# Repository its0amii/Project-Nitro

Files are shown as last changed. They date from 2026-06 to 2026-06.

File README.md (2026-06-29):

# Project-Nitro 🏎️💨

### FPV RC Racing Car with Game Effects

Have you ever wondered about having a **FPV RC Racing Car** with game effects such as:
- Boost
- Gun
- Health
- Drift (Bad effects and more)

Well, I have made this with the help of **NFC TAGS**. How it works is simple: when each car has an NFC reader underneath, and when it passes over a NFC tag, it will detect the code and look for what power or bad effect it is. Then I can pull that effect whenever we want. Beat your opponent and win with super powers using our own strategy to win the game!

## Zine
[zine](/doc/zine.pdf)
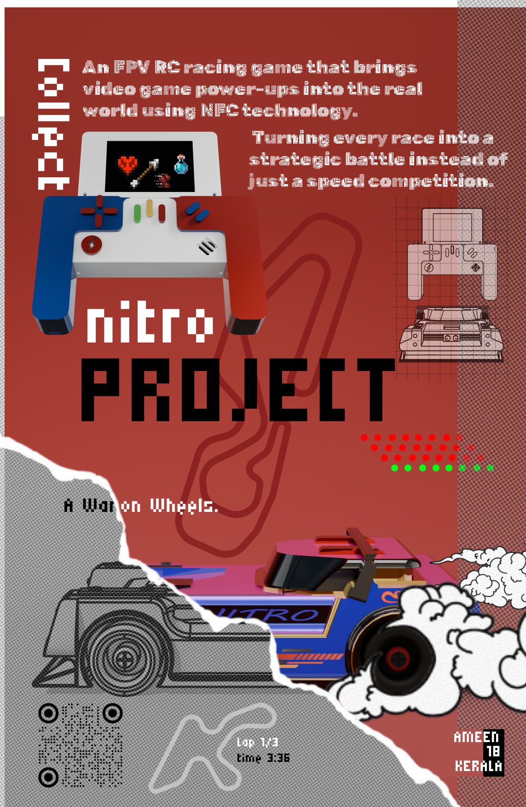
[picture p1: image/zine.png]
zine

## Photos of Car and Remote 📸

### Car Pics

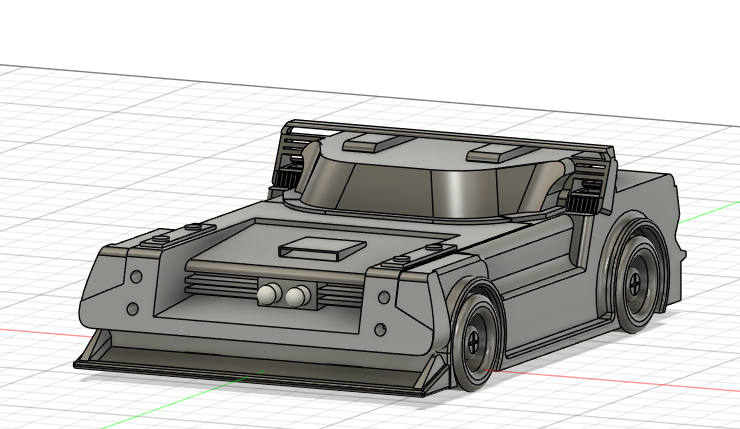
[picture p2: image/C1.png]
Car
  
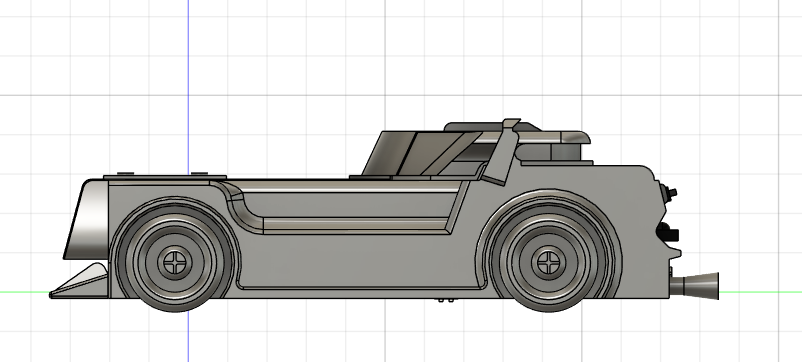
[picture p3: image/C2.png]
Car 2
  
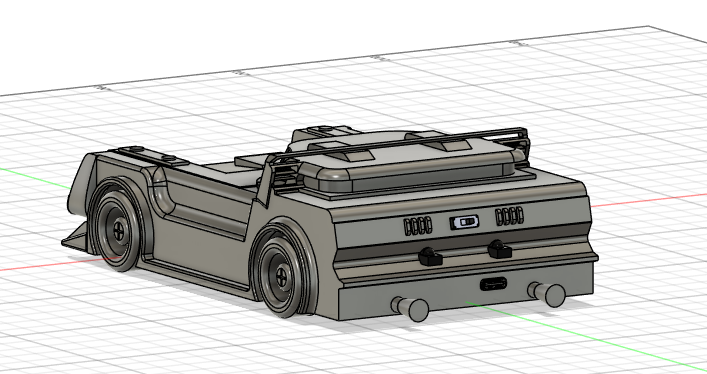
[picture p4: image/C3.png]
Car 3


### Remote

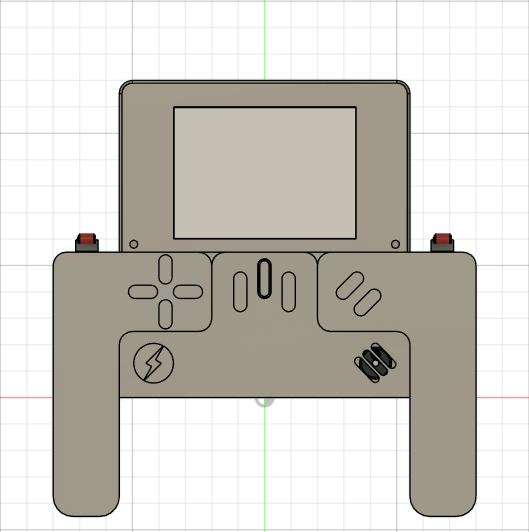
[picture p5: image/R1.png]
Remote
  
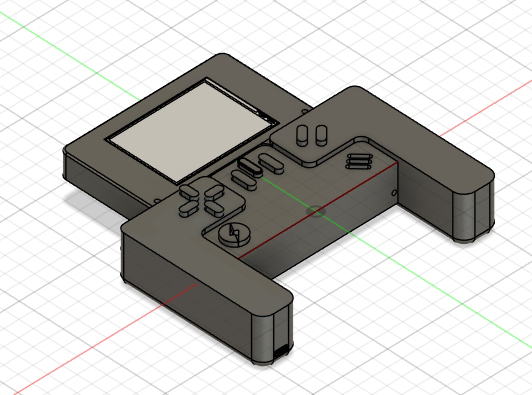
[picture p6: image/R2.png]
Remote 2
  
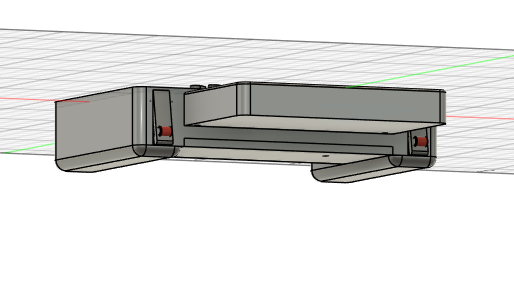
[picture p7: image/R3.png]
Remote 3

## Circuit Diagram

### Car PCB

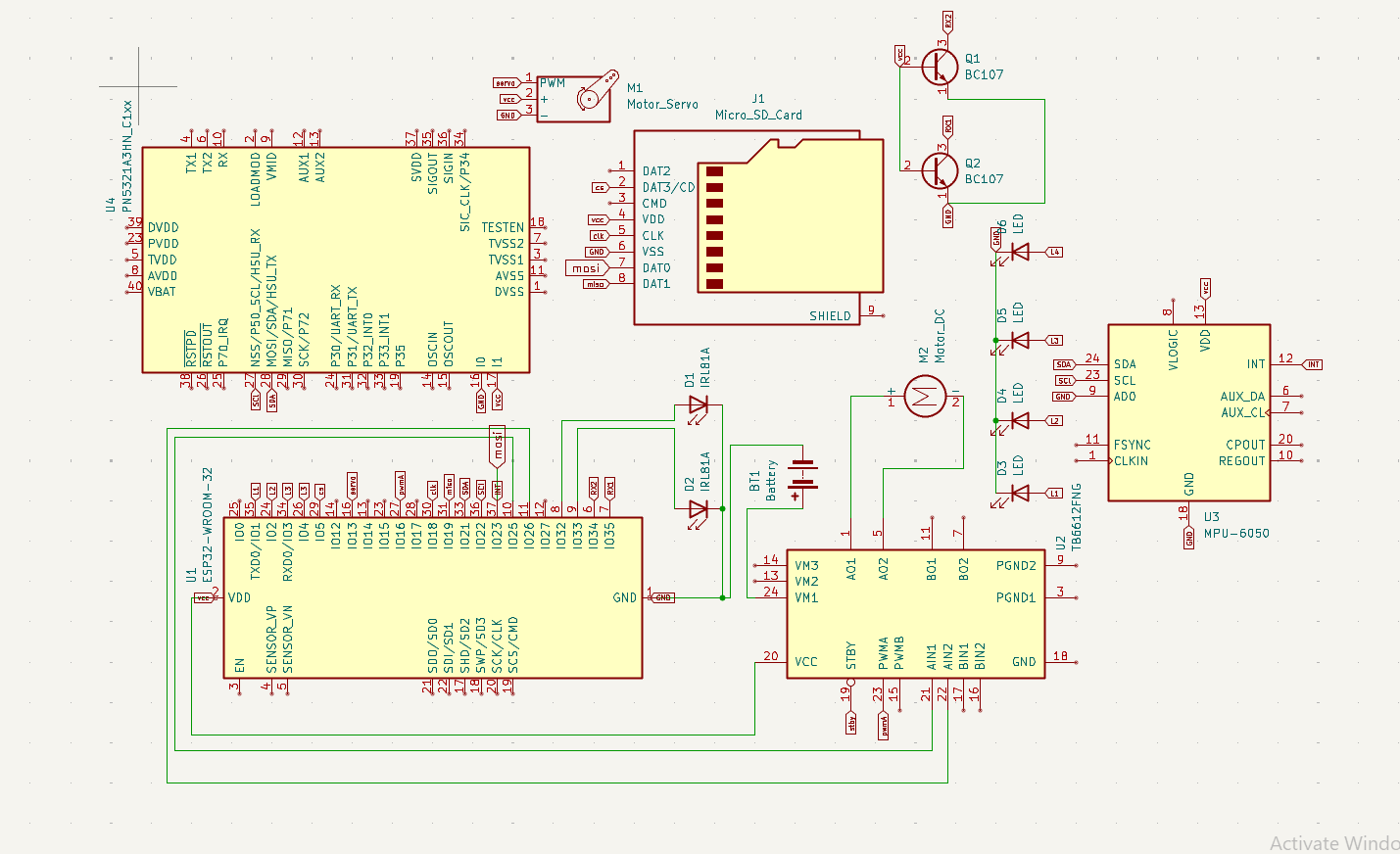
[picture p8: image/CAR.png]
Car PCB


### Remote PCB

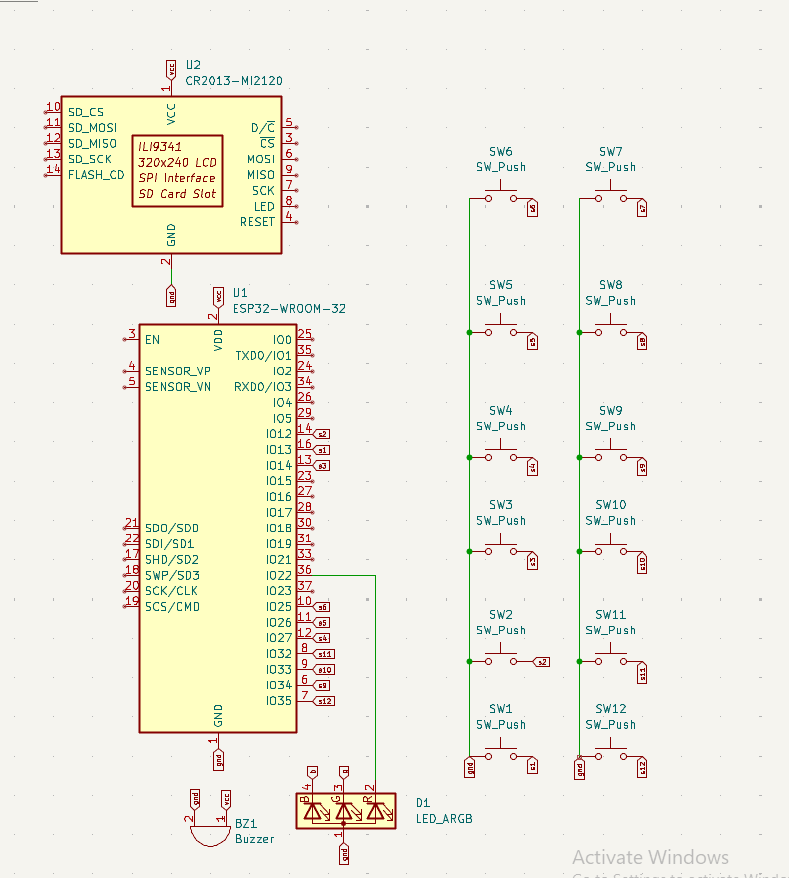
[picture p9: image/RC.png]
Remote PCB
  
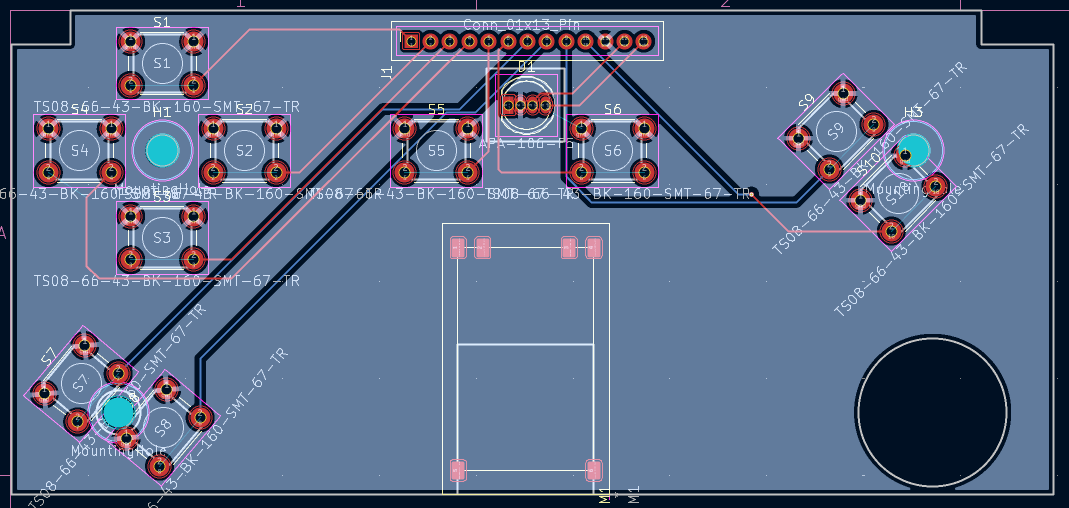
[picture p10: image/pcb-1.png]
PCB 1
  
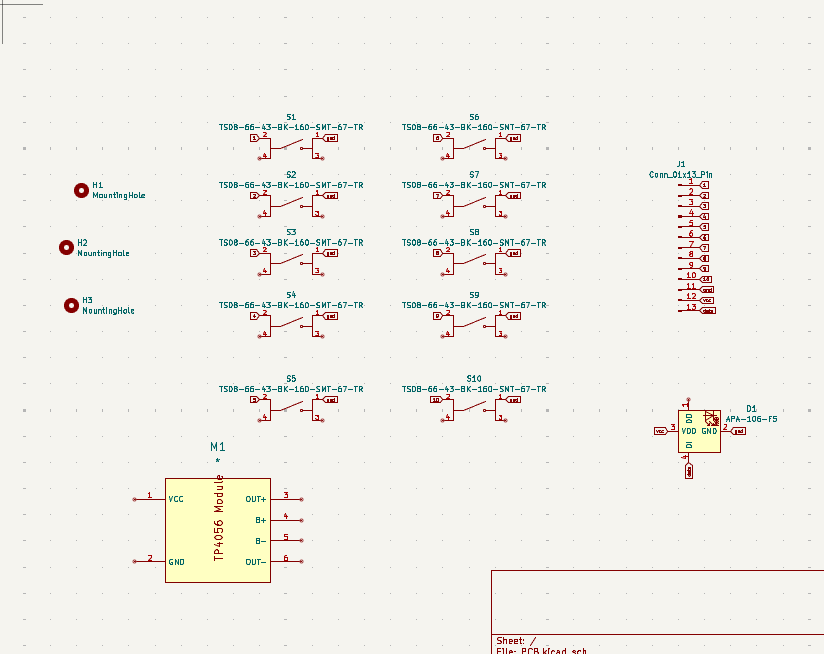
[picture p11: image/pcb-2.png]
PCB 2


## Motivation

I have always wondered to play **RC car** like in games with boost, power, win, health etc.. because that all make more fun for the world and playing with friends makes it even more fun. So I built this car - it will give you a game vibe with RC FPV cars in real life, bringing more fun and joy to the world!
## How to Build 🛠️

### Car Assembly

After 3D printing, check the tolerance of each part and sand it smoothly for better look and placement. Then solder everything with wires, place each component in its designated position as shown in the `.step` files, glue the IR receiver and transmitter, tape or glue the batteries in their places, place ESP32 on the ESP tray and screw it well, then mount to the car body as shown.
## Car Assembly

1. 3D print all STL files from `/cad/car`.
2. Sand the parts until they fit smoothly.
3. Insert all M3 heat inserts
4. Mount the N20 motor using two M3 screws.
5. Install the steering servo.
6. Mount the ESP32.
7. Install the PN532 NFC module.
8. Connect all electronics according to wiring diagram.
9. Mount FPV cam.
10. Install battery
11. scraw body

### Remote Assembly
## Car Assembly

1. 3D print all STL files from `/cad/remote`.
2. Sand the parts until they fit smoothly.
3. Insert all M3 heat inserts.
4. place the batter.
5. Mound the ESP32.
6. Mount PCB after soldering all switchs and LED.
7. Insert the button.
8. Connect all electronics according to wiring diagram.
9. Slide in the sreen and screw.
10. Slide the bottom case.
11. Close body.

After 3D printing, check the tolerance of each part and sand it smoothly for better look and placement. Then solder everything with wires, place the battery first followed by ESP32, solder the switch to PCB and connect the GPIOs Don't forget to place the LCD screen holders to screw for better holding, slide down the bottom part and screw it also then paint everything.

## How to Play/Setup 🎮

When you turn on the remote and car, it will connect (if it's your first time,you may need to pair them) You'll get a web interface in phone or laptop for FPV. Once connected you have two modes:

### Free Ride Mode
You can drive it as normal RC car without any special features.

### Race Mode  
In this mode, you need an opponent to play with. One of you will host the game and that person's car becomes the controller of the game also. The remote looks for players  when a player is found:
- Flip the car and reegister all NFC tags again
- Accept the win gate tag and pit lane
- Place everthing in place as you want
- Everywhere, you can make your own track with anything you have
- Play and win the game
## Game Effects ⚡

### Good Power-ups
- **Boost** - Speed boost to move faster  
- **Health** - Get more health  
- **Shield** - Protection from enemy bullets  
- **Bullets** - Shoot projectiles  

### Bad Effects
- **Drift** - The car gets drift randomly  
- **Random Control** - Controls switch randomly (forward becomes backward)  
- **Slowness** - Car goes slowly  
- **Damage** - Low health  

### Bonus Feature
All bad effects can be cleared by going to your own pit lane.
## How It Works ⚙️

This all works with ESP-NOW protocol. The host's car maintains the rules and everything:

- `car ↔ remote` - Direct communication between each unit  
- `car(host) ↔ car(client)` - Host communicates with client cars  
- `camera → WiFi web → phone, laptop...` - Video stream to viewer devices

## Folder Structure 📁
```
cad/

├── car/
│   └── car.step

├── remote/
│   └── Remote.step

├── nfc/
│   └── nfc tag sticker.step

firmware/

├── car/
│   └── Car firmware

├── remote/
│   └── Remote firmware

├── camera/
│   └── FPV camera firmware
```

### Car Section
- [Car CAD](/cad/car/) - 3D models and designs  
- [Car Firmware](/firmware/car/) - Embedded code for the Car  
- [FPV Camera](/firmware/car_cam/) - Camera firmware  
- [Car Circuit](/circuit/car/) - Schematic diagrams  

### Remote Section
- [Remote CAD](/cad/remote/) - 3D models and designs  
- [Remote Firmware](/firmware/remote/) - Embedded code for the remote  
- [Remote circuit](/circuit/remote/) - Schematic diagrams

## BOM (Bill of Material)
[BOM](/doc/BOM.csv.csv)

## Car Components 🛒

|**Item**|Number|Approx. Price|Link|
|---|---|---|---|
|5mm 940nm IR Emitter Transmitter|2|₹140|[Amazon](https://amzn.in/d/03gj3whx)|
|MPU6050 IMU|1|₹174|[Amaz](https://amzn.in/d/0gS9H64g)|
|PN532 NFC RFID Module|1|₹425|[Robokit](https://robokits.co.in/wireless-solutions/rfid/pn532-nfc-rfid-module-v3-kit-reader-writer-breakout-board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)|
|ESP32S3-Sense|1|₹1800|[SeeedStudio](https://www.seeedstudio.com/XIAO-ESP32S3-Sense-p-5639.html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)|
|ESP32 WiFi Bluetooth|1|₹299|[Amazon](https://amzn.in/d/0fkaqaUV)|
|6V N20 600 RPM Motor|1|₹149|[Robocraz](https://robocraze.com/products/6v-n20-600-rpm-miniature-gear-motor)|
|3.7V 2500mAh 18650 Li-Ion Battery|2|₹500|[Robocraze](https://robocraze.com/products/3-7v-2500mah-18650-li-ion-battery)|
|TP4056 Type-C Mini Charger|1|₹49|[Robocraz](https://robocraze.com/products/tp4056-battery-charger-c-type-module-with-protection-1)|
|LM2596 DC-DC Buck Converter|1|₹79|[Robocraze](https://robocraze.com/products/lm2596-dc-dc-buck-module)|
|SG90 Micro Servo Motor|1|₹99|[robocraze](https://robocraze.com/products/sg90-micro-servo-motor)|
|DRV8833 2-Channel Driver|1|₹99|[Robocraze](https://robocraze.com/products/drv8833-2-channel-dc-motor-driver)|
|TSOP38238 IR Receiver Diode|2|₹50|[QuartzComponents](https://quartzcomponents.com/products/tsop38238-ir-receiver-diode-38khz)|
|M3x4mm Heat Set Inserts|20|₹80|[Robu](https://robu.in/product/m3-x-4-mm-brass-heat-set-knurl-threaded-round-insert-nut-25-pcs/)|
|M3 x 6mm Screw|20|₹60|[RoboticsDNA](roboticsdna.in/product/m3-x-6mm-bolt-ss-304-csk-countersunk-philips-head-25-pcs/)|

#### Approximate Car Cost: **₹4,000**

### Remote

|**Item**|Number|Approx. Price|Link|
|---|-----|---|---|
|ESP32 WiFi Bluetooth|1|₹299|[Amazon](https://amzn.in/d/03HUoLg3)|
|Tactile momentary push button|12|₹36|[amazon](https://amzn.in/d/093r9Vyk)|
|3.7V 1500mAh LiPo Rechargeable Battery Model|1|₹350|[robocraze](https://robocraze.com/products/3-7v-1500mah-lipo-rechargeable-battery-model-uk-523450p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)|
|TP4056 Type-C Mini|1|₹49|[robocraze](https://robocraze.com/products/tp4056-battery-charger-c-type-module-with-protection-1)|
|3.3V Small Piezo Buzzer|1|₹30|https://robocraze.com/products/3-volts-buzzer-small|
|5mm Common Anode RGB LED 4Pin Through Hole White Diffused LED|1|₹15|[robocraze](https://robocraze.com/products/5mm-common-anode-rgb-led-4pin-pack-of-10)|
|2.8 Inch TFT LCD Display|1|₹780|[robocraze](https://robocraze.com/products/smartelex-2-8-inch-tft-lcd-display-240x320-color-lcd-screen-for-diy-electronics)|
|m3x4mm heat set inserts|12|₹80|[Rubu](https://robu.in/product)|m3-x-4-mm-brass-heat-set-knurl-threaded-round-insert-nut-25-pcs/|
|M3 x 6mm screw|12|₹60|[RoboticsDNA](roboticsdna.in/product/m3-x-6mm-bolt-ss-304-csk-countersunk-philips-head-25-pcs/)
#### Approximate Remote Cost
**₹1700**

### Total Approximate Cost

|Part|Cost|
|-----|-----|
|Car|₹4000|
|Remote|₹1700|

# Future Upgrade ⏫

* Leader Board 
* Anti-Cheat
* challenge etc

Thats it for now.
> **NOTE:** you need to place a black transparent plastic thin sheet or something on the front window where the camera is placed and in the remote for the switch you can either use this Prototyping PCB or you can custom print a pcb board everything on car and remote is either snap fit or screwable and only the led , ir and batter need glue-gun/tap

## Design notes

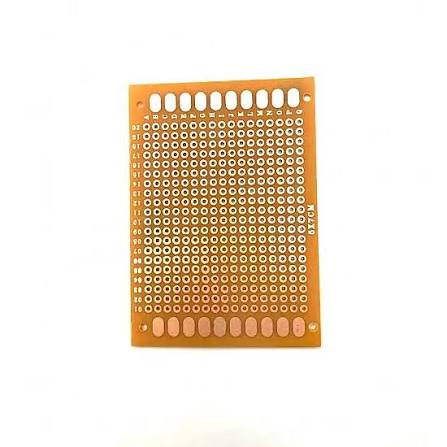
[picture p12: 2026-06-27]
image/image.png

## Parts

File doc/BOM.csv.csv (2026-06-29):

Category | Item | Quantity | Approx_Price_INR | Link
Car | 5mm 940nm IR Emitter Transmitter | 2 | 140 | https://amzn.in/d/03gj3whx
Car | MPU6050 IMU | 1 | 174 | https://amzn.in/d/0gS9H64g
Car | PN532 NFC RFID Module | 1 | 425 | https://robokits.co.in/wireless-solutions/rfid/pn532-nfc-rfid-module-v3-kit-reader-writer-breakout-board
Car | ESP32S3-Sense | 1 | 1800 | https://www.seeedstudio.com/XIAO-ESP32S3-Sense-p-5639.html
Car | ESP32 WiFi Bluetooth | 1 | 299 | https://amzn.in/d/0fkaqaUV
Car | 6V N20 600 RPM Motor | 1 | 149 | https://robocraze.com/products/6v-n20-600-rpm-miniature-gear-motor
Car | 3.7V 2500mAh 18650 Li-Ion Battery | 2 | 500 | https://robocraze.com/products/3-7v-2500mah-18650-li-ion-battery
Car | TP4056 Battery Charger | 1 | 49 | https://robocraze.com/products/tp4056-battery-charger-c-type-module-with-protection-1
Car | LM2596 DC-DC Buck Converter | 1 | 79 | https://robocraze.com/products/lm2596-dc-dc-buck-module
Car | SG90 Micro Servo Motor | 1 | 99 | https://robocraze.com/products/sg90-micro-servo-motor
Car | DRV8833 Motor Driver | 1 | 99 | https://robocraze.com/products/drv8833-2-channel-dc-motor-driver
Car | TSOP38238 IR Receiver Diode | 2 | 50 | https://quartzcomponents.com/products/tsop38238-ir-receiver-diode-38khz
Car | M3x4mm Heat Set Inserts | 20 | 50
Car | M3x6mm Screws | 20 | 50
Remote | ESP32 WiFi Bluetooth | 1 | 299 | https://amzn.in/d/03HUoLg3
Remote | Tactile Momentary Push Button | 12 | 36 | https://amzn.in/d/093r9Vyk
Remote | 3.7V 1500mAh LiPo Battery | 1 | 350 | https://robocraze.com/products/3-7v-1500mah-lipo-rechargeable-battery-model-uk-523450p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
Remote | TP4056 Battery Charger | 1 | 49 | https://robocraze.com/products/tp4056-battery-charger-c-type-module-with-protection-1
Remote | 3.3V Small Piezo Buzzer | 1 | 30 | https://robocraze.com/products/3-volts-buzzer-small
Remote | 5mm Common Anode RGB LED | 1 | 15 | https://robocraze.com/products/5mm-common-anode-rgb-led-4pin-pack-of-10
Remote | 2.8 Inch TFT LCD Display | 1 | 780 | https://robocraze.com/products/smartelex-2-8-inch-tft-lcd-display-240x320-color-lcd-screen-for-diy-electronics
Remote | M3x4mm Heat Set Inserts | 12 | 30
Remote | M3x6mm Screws | 12 | 30
SUMMARY | Car Total |  | 3963
SUMMARY | Remote Total |  | 1619
SUMMARY | Grand Total |  | 5582

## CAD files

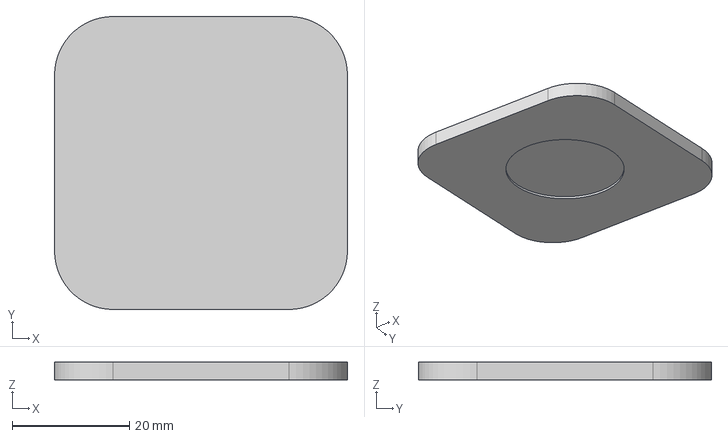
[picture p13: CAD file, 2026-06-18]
cad/nfc/nfc tag sticker.step
50.0 x 50.0 x 3.00 mm

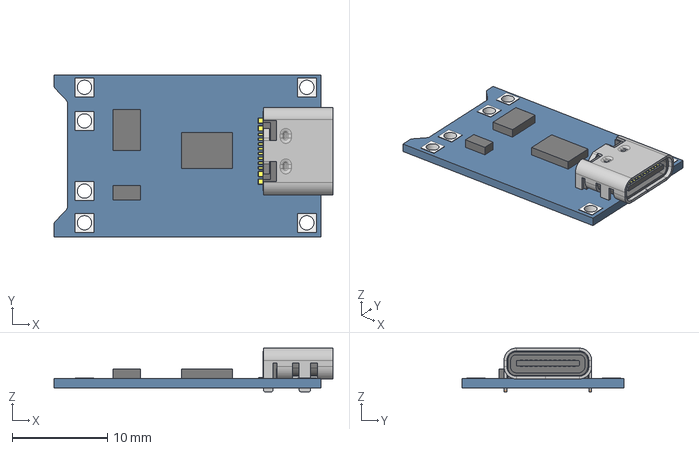
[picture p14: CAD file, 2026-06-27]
pcb/rc/footprint-symbol/TP4056--3DModel-STEP-684600.STEP
29.3 x 17.0 x 4.60 mm

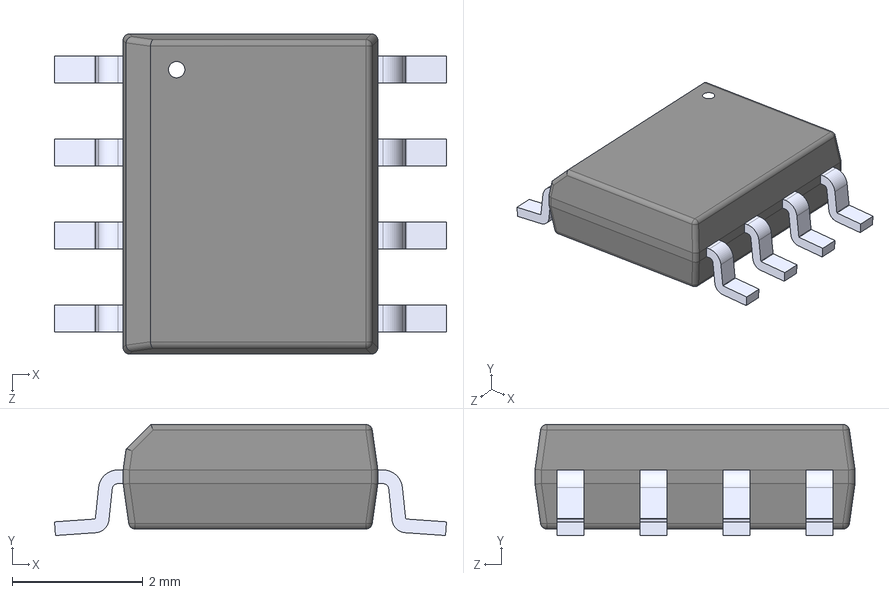
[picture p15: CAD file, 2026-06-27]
pcb/rc/footprint-symbol/TP4056/TP4056.step
6.00 x 1.70 x 4.90 mm

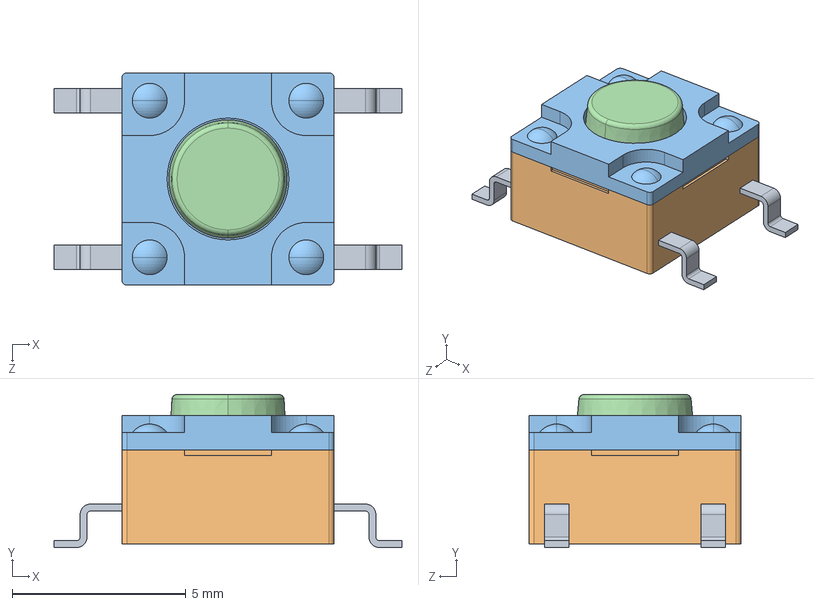
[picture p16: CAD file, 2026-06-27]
pcb/rc/footprint-symbol/TS08-66-43-BK-160-SMT-67-TR/TS08-66-43-BK-160-SMT-67-TR.step
10.0 x 4.40 x 6.10 mm

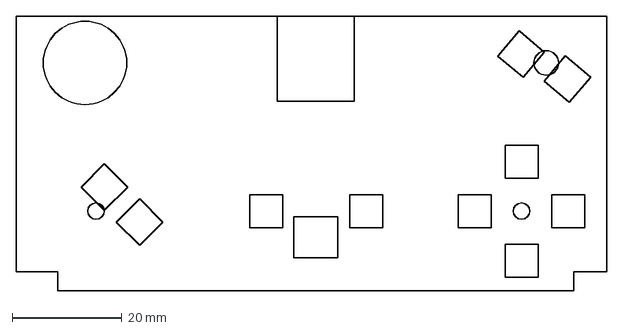
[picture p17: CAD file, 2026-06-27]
pcb/rc/Sketch.dxf
107.5 x 50.0 mm

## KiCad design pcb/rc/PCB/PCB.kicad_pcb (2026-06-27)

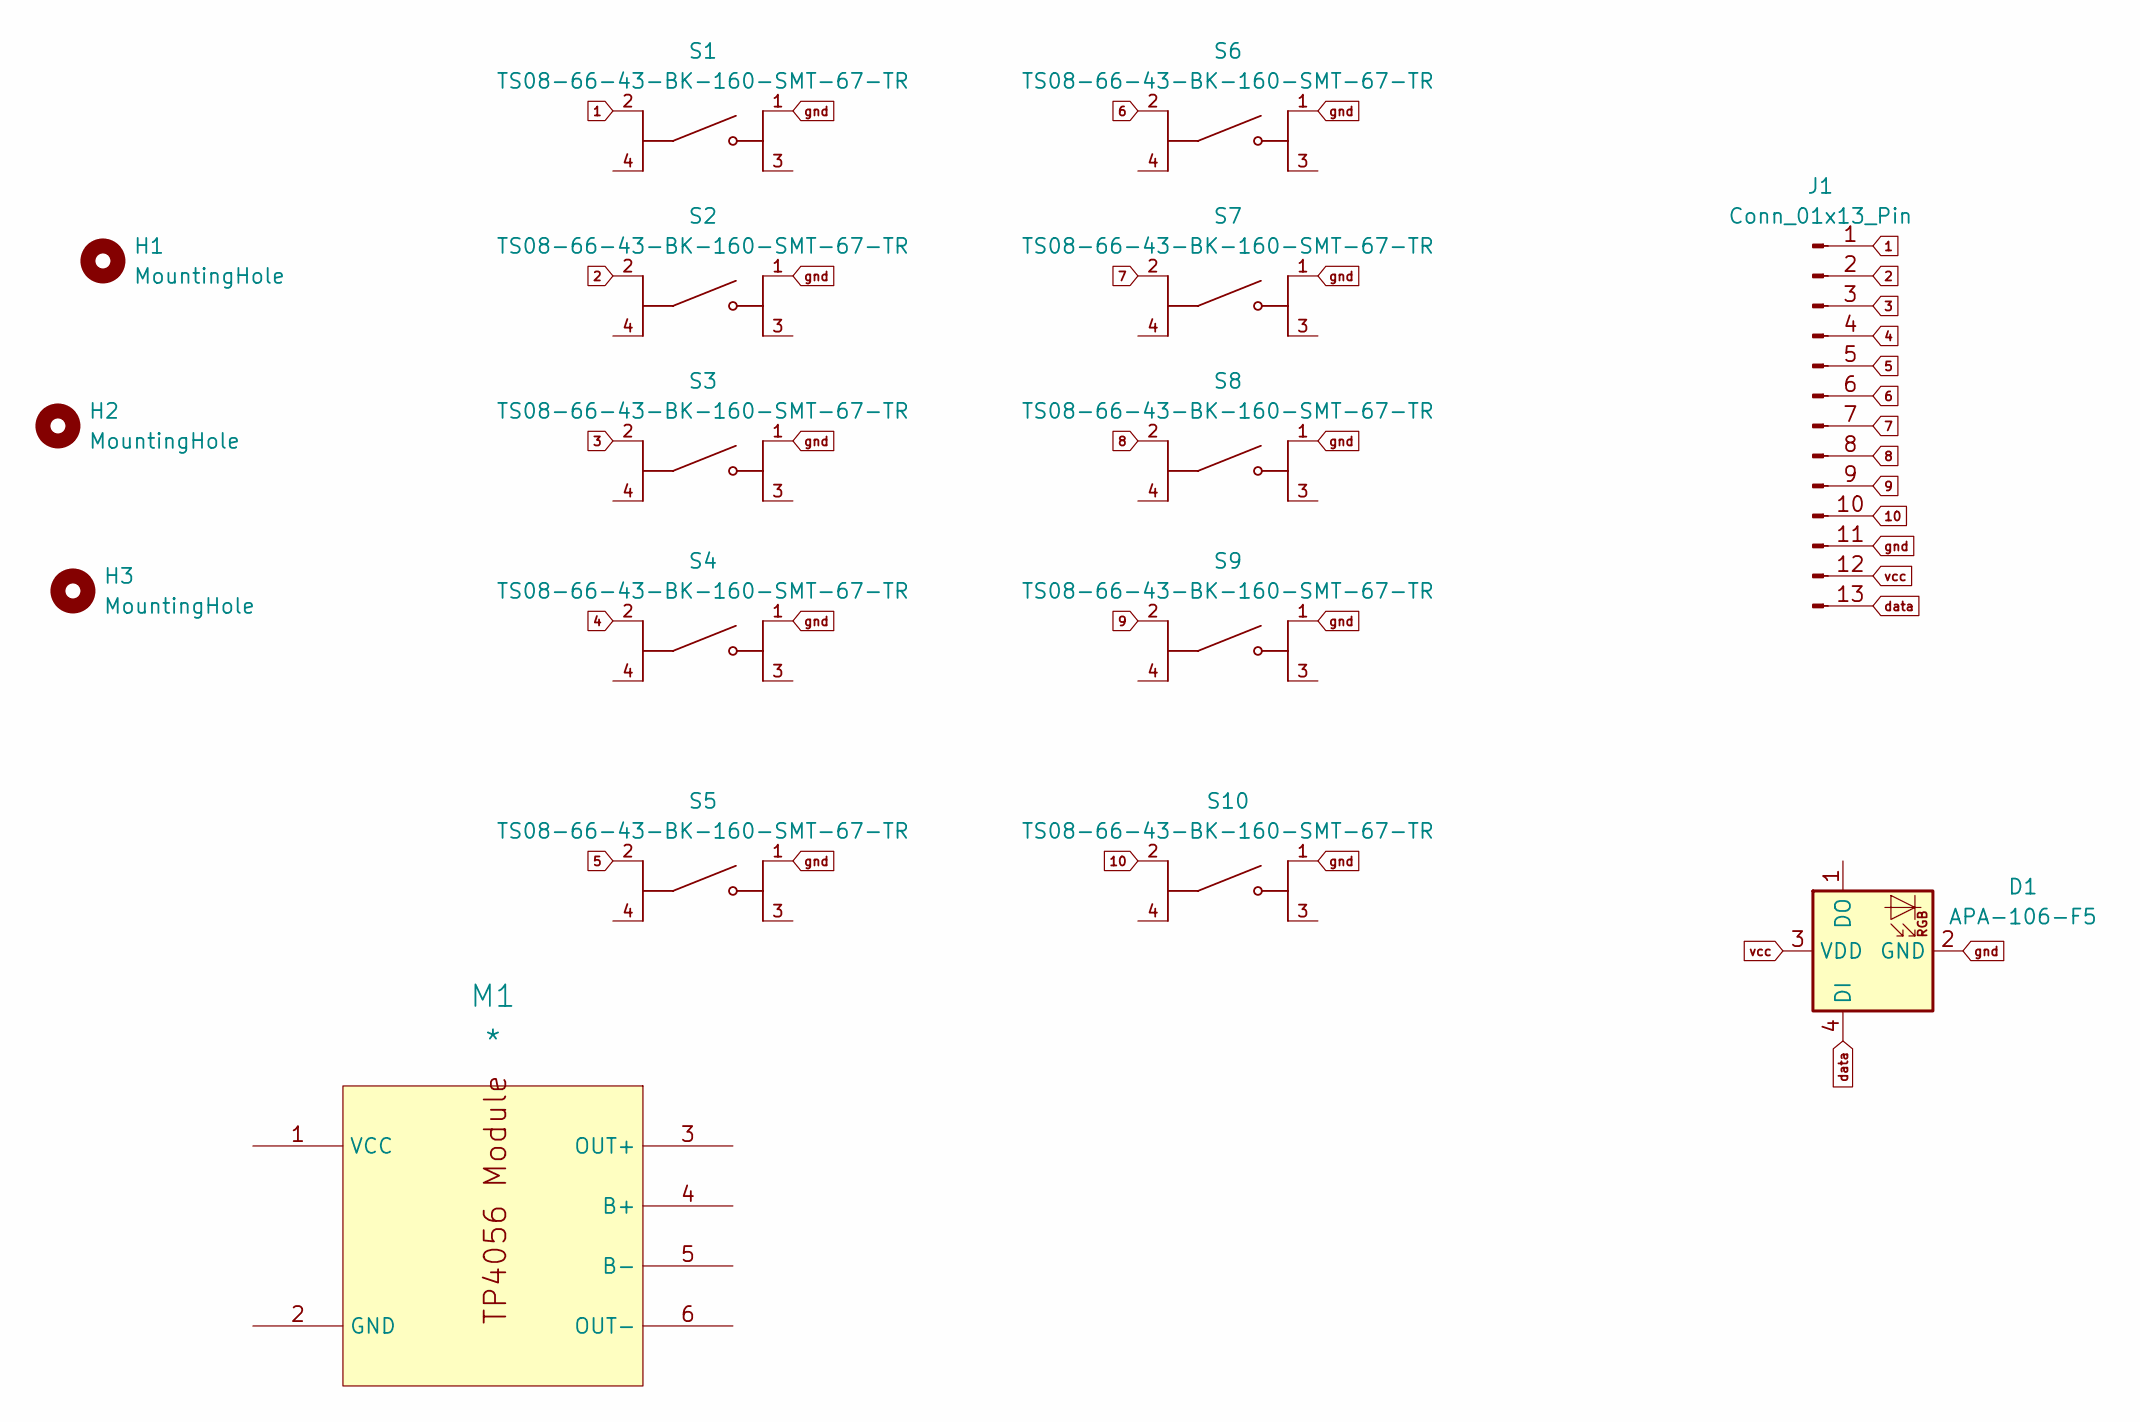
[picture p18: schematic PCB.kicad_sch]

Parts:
D1: APA-106-F5; LED_D5.0mm-4_RGB
H1, H2, H3: MountingHole; MountingHole_3mm
J1: Conn_01x13_Pin; PinSocket_1x13_P2.00mm_Horizontal
M1: *; tp4056
S1, S2, S3, S4, S5, S6, S7, S8, S9, S10: TS08-66-43-BK-160-SMT-67-TR; SW_PUSH_6mm; PARTREV 1.03

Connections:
1: J1.1, S1.2
2: J1.2, S2.2
3: J1.3, S3.2
4: J1.4, S4.2
5: J1.5, S5.2
6: J1.6, S6.2
7: J1.7, S7.2
8: J1.8, S8.2
9: J1.9, S9.2
10: J1.10, S10.2
data: D1.4 (DI), J1.13
gnd: D1.2 (GND), J1.11, S1.1, S2.1, S3.1, S4.1, S5.1, S6.1, S7.1, S8.1, S9.1, S10.1
vcc: D1.3 (VDD), J1.12

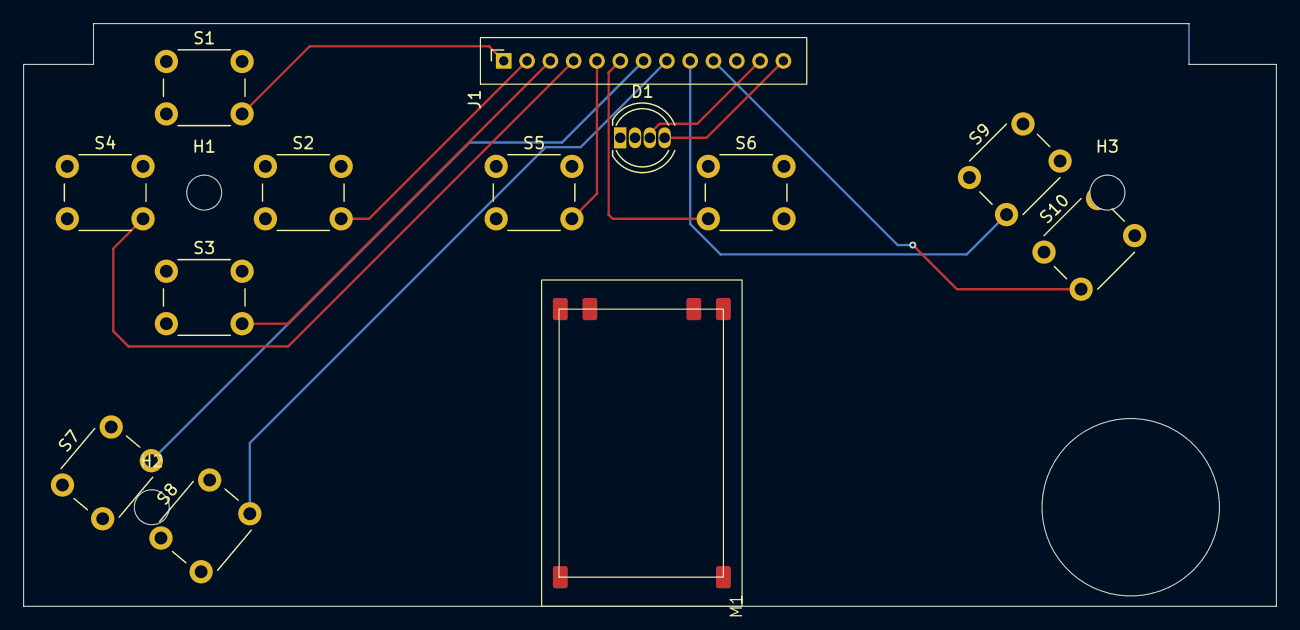
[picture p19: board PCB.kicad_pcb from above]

Board: 2 copper layers, 107.5 x 50.0 mm, 16 parts (0 on the bottom side), 13 nets.

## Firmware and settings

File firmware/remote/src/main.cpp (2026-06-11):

// =============================================================================
//  main.cpp — FPV Racer v2.0 RC Firmware
//
//  ESP32 30-pin, 2.8" ILI9341 TFT (SPI), 12 buttons
//
//  Core 0 (app_cpu): loop() — ESP-NOW receive, phase state machine,
//                             button events, display updates
//  Core 1 (pro_cpu): driveTask — 50Hz drive packet sender
//
//  Power-on sequence:
//    1. MCU wakes → PWR_LATCH HIGH (holds own power via P-MOSFET)
//    2. Splash screen
//    3. Attempt to connect to paired car (stored MAC in NVS)
//    4. RC_IDLE / RC_FREE_DRIVE
//    5. CONNECT button → RC_LOOKING → pairing → lobby → race
// =============================================================================

#include <Arduino.h>
#include <WiFi.h>
#include <esp_now.h>
#include <Preferences.h>
#include <freertos/FreeRTOS.h>
#include <freertos/task.h>
#include <freertos/queue.h>
#include <freertos/semphr.h>

#include "rc_types.h"
#include "buttons.h"
#include "rc_display.h"

// ---------------------------------------------------------------------------
// Global state
// ---------------------------------------------------------------------------
static RCPhase      g_phase       = RC_IDLE;
static RCGameState  g_gs          = {};
static bool         g_carConnected= false;
static bool         g_isHost      = false; // RC paired to host car?

// Peer MACs
static uint8_t g_ownMac[6]    = {};
static uint8_t g_carMac[6]    = {};      // paired car
static uint8_t g_oppCarMac[6] = {};      // opponent car (host for validation)
static uint8_t g_oppRcMac[6]  = {};      // opponent RC
static bool    g_peersKnown   = false;

// Lobby settings (host RC only)
static uint8_t  g_lobbyMode  = 0;   // 0=LAP, 1=TIME
static uint8_t  g_lobbyLaps  = 5;
static uint16_t g_lobbyTimeSec = 180;
static uint8_t  g_lobbyTags  = 10;
static bool     g_myReady    = false;
static bool     g_oppReady   = false;

// Battery %
static uint8_t  g_battPct    = 100;

// Match end packet
static PktMatchEnd g_matchEnd = {};

// ---------------------------------------------------------------------------
// FreeRTOS
// ---------------------------------------------------------------------------
static QueueHandle_t     xRxQueue;      // ESP-NOW → Core 0
static SemaphoreHandle_t xDriveSem;     // Core 0 → Core 1: ok to send drive

// Drive command (written by Core 0, read by Core 1)
static volatile int8_t g_driveThrottle = 0;
static volatile int8_t g_driveSteering = 0;

// Last shoot time
static uint32_t g_lastShootMs = 0;

// Looking animation
static uint8_t  g_lookingDot  = 0;
static uint32_t g_lookingMs   = 0;
static uint32_t g_lookingStartMs = 0;

// NFC setup state (mirrored from car via UI updates)
static uint8_t g_nfcDone  = 0;
static uint8_t g_nfcTotal = 10;

// ---------------------------------------------------------------------------
// ESP-NOW helpers
// ---------------------------------------------------------------------------

static esp_now_peer_info_t s_peer = {};

static void espnow_add_peer(const uint8_t* mac) {
    memcpy(s_peer.peer_addr, mac, 6);
    s_peer.channel = 0;
    s_peer.encrypt = false;
    if (!esp_now_is_peer_exist(mac))
        esp_now_add_peer(&s_peer);
}

static void espnow_send(const uint8_t* mac, const void* data, size_t len) {
    if (esp_now_is_peer_exist(mac))
        esp_now_send(mac, (const uint8_t*)data, len);
}

static void espnow_broadcast(const void* data, size_t len) {
    // ESP-NOW broadcast MAC
    static const uint8_t bcast[6] = {0xFF,0xFF,0xFF,0xFF,0xFF,0xFF};
    esp_now_send(bcast, (const uint8_t*)data, len);
}

// ESP-NOW receive ISR — enqueue raw packet
static void on_recv(const uint8_t* mac, const uint8_t* data, int len) {
    IncomingPacket pkt;
    memcpy(pkt.senderMac, mac, 6);
    pkt.len = (len > 250) ? 250 : len;
    memcpy(pkt.data, data, pkt.len);
    xQueueSendFromISR(xRxQueue, &pkt, nullptr);
}

// ---------------------------------------------------------------------------
// Battery ADC (read when buttons known idle)
// ---------------------------------------------------------------------------
static uint8_t read_battery_pct() {
    // Voltage divider: 100kΩ + 100kΩ → pin 34, Vref 3.3V
    // LiPo: 4.2V = 100%, 3.0V = 0%
    // At pin: 4.2V → 2.1V → ADC = 2610; 3.0V → 1.5V → ADC = 1861
    int raw = analogRead(PIN_BATT_ADC);
    int mv  = (int)((long)raw * 3300 / 4095) * 2; // × 2 for divider
    int pct = (mv - 3000) * 100 / (4200 - 3000);
    return (uint8_t)constrain(pct, 0, 100);
}

// ---------------------------------------------------------------------------
// Send drive packet (called from Core 1 driveTask at 50Hz)
// ---------------------------------------------------------------------------
static void send_drive(int8_t thr, int8_t str) {
    if (!g_carConnected) return;
    if (g_phase != RC_RACING && g_phase != RC_FREE_DRIVE) return;
    PktDrive pkt;
    pkt.hdr = { PKT_DRIVE, RC_ID, (uint32_t)millis() };
    pkt.throttle = thr;
    pkt.steering = str;
    espnow_send(g_carMac, &pkt, sizeof(pkt));
}

// ---------------------------------------------------------------------------
// Core 1 — Drive Task (50Hz)
// ---------------------------------------------------------------------------
static void driveTask(void* pv) {
    while (true) {
        int8_t thr = 0, str = 0;

        // Read held buttons for throttle
        if (buttons_held(BTN_ID_UP))    thr =  80;
        if (buttons_held(BTN_ID_DOWN))  thr = -60;
        if (buttons_held(BTN_ID_LEFT))  str = -80;
        if (buttons_held(BTN_ID_RIGHT)) str =  80;

        // Diagonal combination — reduce throttle for tighter turns
        if (str != 0 && thr != 0) thr = (int8_t)(thr * 80 / 100);

        g_driveThrottle = thr;
        g_driveSteering = str;
        send_drive(thr, str);

        vTaskDelay(pdMS_TO_TICKS(DRIVE_RATE_MS)); // 50Hz
    }
}

// ---------------------------------------------------------------------------
// Packet dispatcher (Core 0)
// ---------------------------------------------------------------------------
static void dispatch(const IncomingPacket& raw) {
    if (raw.len < sizeof(PktHeader)) return;
    const PktHeader* hdr = (const PktHeader*)raw.data;
    uint32_t now = millis();

    switch (hdr->type) {

        // ── UI state from host car — primary game state update ─────────────
        case PKT_UI_STATE: {
            const PktUIState* us = (const PktUIState*)raw.data;
            bool hpChanged  = (us->ui.myHealth  != g_gs.myHealth  ||
                               us->ui.oppHealth != g_gs.oppHealth);
            bool lapChanged = (us->ui.myLaps    != g_gs.myLaps);
            bool invChanged = false;
            for (int i = 0; i < 4; i++)
                if ((PowerType)us->ui.activePower[i] != g_gs.inventory[i])
                    invChanged = true;
            bool badChanged = (us->ui.badPower != (uint8_t)g_gs.badPower);
            bool timChanged = (us->ui.countdown != g_gs.countdown);

            // Copy state
            g_gs.myHealth  = us->ui.myHealth;
            g_gs.oppHealth = us->ui.oppHealth;
            g_gs.myBullets = us->ui.myBullets;
            g_gs.myLaps    = us->ui.myLaps;
            g_gs.oppLaps   = us->ui.oppLaps;
            g_gs.myScore   = us->ui.myScore;
            g_gs.oppScore  = us->ui.oppScore;
            g_gs.badPower  = (PowerType)us->ui.badPower;
            g_gs.countdown = us->ui.countdown;
            g_gs.matchTimeMs = us->ui.matchTimeMs;
            g_gs.flags     = us->ui.flags;
            for (int i = 0; i < 4; i++)
                g_gs.inventory[i] = (PowerType)us->ui.activePower[i];

            if (hpChanged)  display_dirty_hp();
            if (invChanged) display_dirty_powers();
            if (badChanged) display_dirty_bad();
            if (timChanged || lapChanged) display_dirty_header();
            break;
        }

        // ── Health update ───────────────────────────────────────────────────
        case PKT_HEALTH_UPD: {
            struct { PktHeader h; uint8_t p1hp; uint8_t p2hp; int8_t delta; uint8_t victim; } *hu =
                (decltype(hu))raw.data;
            g_gs.myHealth  = (RC_ID == 1) ? hu->p1hp : hu->p2hp;
            g_gs.oppHealth = (RC_ID == 1) ? hu->p2hp : hu->p1hp;
            display_dirty_hp();

            // Log message
            char msg[32];
            if (hu->delta < 0) {
                snprintf(msg, sizeof(msg), "HIT -%d HP!", -hu->delta);
                display_push_log(msg);
                // Buzzer beep — TODO: hw_buzzer_beep(400, 100)
            } else {
                snprintf(msg, sizeof(msg), "REGEN +%d HP", hu->delta);
                display_push_log(msg);
            }
            break;
        }

        // ── Bullet count update ─────────────────────────────────────────────
        case PKT_BULLET_UPD: {
            // Bullets embedded in next UIState; force redraw now
            display_dirty_powers();
            break;
        }

        // ── Power granted (tag pickup) ──────────────────────────────────────
        case PKT_GRANT: {
            display_dirty_powers();
            display_push_log("TAG! Power gained");
            // Buzzer: 1000Hz 80ms — TODO
            break;
        }

        // ── Host denied event ───────────────────────────────────────────────
        case PKT_DENY: {
            display_push_log("Action DENIED");
            // Buzzer: 200Hz 200ms — TODO
            break;
        }

        // ── Shield absorbed ─────────────────────────────────────────────────
        case PKT_SHIELD_ABS: {
            display_push_log("SHIELD absorbed hit!");
            display_dirty_hp();
            break;
        }

        // ── Apply bad power ─────────────────────────────────────────────────
        case PKT_APPLY_BAD: {
            const PktApplyBad* ab = (const PktApplyBad*)raw.data;
            g_gs.badPower = ab->badType;
            display_set_bad_timer(ab->timeoutMs);
            display_dirty_bad();
            char msg[32];
            snprintf(msg, sizeof(msg), "BAD: %s!", power_name_rc(ab->badType));
            display_push_log(msg);
            // Buzzer: 300Hz 400ms — TODO
            break;
        }

        // ── Clear bad power ─────────────────────────────────────────────────
        case PKT_CLEAR_BAD: {
            g_gs.badPower = PWR_NONE;
            display_set_bad_timer(0);
            display_dirty_bad();
            display_push_log("Bad power CURED");
            break;
        }

        // ── Execute good power (feedback only — car does the physics) ────────
        case PKT_EXECUTE: {
            struct { PktHeader h; uint8_t pwr; uint32_t dur; } *ex = (decltype(ex))raw.data;
            char msg[32];
            snprintf(msg, sizeof(msg), "POWER: %s!", power_name_rc((PowerType)ex->pwr));
            display_push_log(msg);
            display_dirty_powers();
            break;
        }

        // ── Global freeze ────────────────────────────────────────────────────
        case PKT_GLOBAL_FREEZE: {
            g_gs.flags |= 0x04;
            display_dirty_full();
            display_push_log("!! FROZEN !!");
            break;
        }
        case PKT_GLOBAL_RESUME: {
            g_gs.flags &= ~0x04;
            display_dirty_full();
            display_push_log("Resumed");
            break;
        }

        // ── Countdown from host ───────────────────────────────────────────────
        case PKT_COUNTDOWN: {
            const PktCountdown* cd = (const PktCountdown*)raw.data;
            g_phase = RC_COUNTDOWN;
            display_countdown(cd->tick);
            if (cd->tick == 0) {
                g_phase = RC_RACING;
                g_gs.phase = 6;
                display_force_full_redraw();
            }
            break;
        }

        // ── Lap update ───────────────────────────────────────────────────────
        case PKT_LAP_UPD: {
            display_dirty_header();
            display_push_log("LAP complete +10");
            break;
        }

        // ── Match end ────────────────────────────────────────────────────────
        case PKT_MATCH_END: {
            g_matchEnd = *(const PktMatchEnd*)raw.data;
            g_phase = RC_FINISHED;
            display_results(&g_matchEnd, RC_ID);
            break;
        }

        // ── Pairing: opponent RC is looking ──────────────────────────────────
        case PKT_RACE_LOOKING: {
            if (g_phase != RC_IDLE && g_phase != RC_FREE_DRIVE) break;
            const PktRaceLooking* lk = (const PktRaceLooking*)raw.data;
            // Show "Accept?" prompt — store their mac
            memcpy(g_oppRcMac, lk->rcMac, 6);
            memcpy(g_oppCarMac, lk->carMac, 6);
            g_phase = RC_WAIT_ACCEPT;
            display_accept_request(lk->hdr.sender);
            break;
        }

        // ── Pairing: opponent accepted our LOOKING ────────────────────────────
        case PKT_RACE_ACCEPT: {
            if (g_phase != RC_LOOKING) break;
            const PktRaceAccept* ac = (const PktRaceAccept*)raw.data;
            memcpy(g_oppRcMac,  ac->rcMac,  6);
            memcpy(g_oppCarMac, ac->carMac, 6);
            espnow_add_peer(g_oppRcMac);
            espnow_add_peer(g_oppCarMac);
            g_peersKnown = true;
            g_isHost     = true; // we initiated → we're the host-side RC
            g_phase      = RC_NFC_SETUP;
            display_force_full_redraw();
            break;
        }

        // ── Settings sync from host RC ────────────────────────────────────────
        case PKT_RACE_SETTINGS: {
            const PktRaceSettings* rs = (const PktRaceSettings*)raw.data;
            g_lobbyMode    = rs->mode;
            g_lobbyLaps    = rs->targetLaps;
            g_lobbyTimeSec = rs->timeLimitS;
            g_lobbyTags    = rs->tagCount;
            display_dirty_full();
            break;
        }

        // ── Ready / Start ─────────────────────────────────────────────────────
        case PKT_READY: {
            g_oppReady = true;
            display_dirty_full();
            break;
        }

        // ── Car heartbeat — confirms connection ───────────────────────────────
        case PKT_HEARTBEAT: {
            g_carConnected = true;
            break;
        }

        default: break;
    }
}

// Helper — power name for RC side (mirrors car firmware's power_name)
static const char* power_name_rc(PowerType p) {
    switch(p) {
        case PWR_BOOST:       return "BOOST";
        case PWR_SHIELD:      return "SHIELD";
        case PWR_REGEN:       return "REGEN";
        case PWR_BULLETS:     return "AMMO+3";
        case BAD_SLOWNESS:    return "SLOW";
        case BAD_RANDOM_CTRL: return "CHAOS";
        case BAD_DAMAGE:      return "DAMAGE";
        case BAD_DRIFT:       return "DRIFT";
        default:              return "???";
    }
}
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
void loop() {
    uint32_t now = millis();

    // ── 1. Drain ESP-NOW receive queue ───────────────────────────────────────
    IncomingPacket pkt;
    while (xQueueReceive(xRxQueue, &pkt, 0) == pdTRUE) {
        dispatch(pkt);
    }

    // ── 2. Button events ─────────────────────────────────────────────────────
    buttons_tick();
    BtnEvent ev;
    while (buttons_poll(&ev)) {
        handle_button(ev);
    }

    // ── 3. Phase-specific periodic logic ─────────────────────────────────────
    switch (g_phase) {

        case RC_IDLE:
        case RC_FREE_DRIVE:
            display_idle(g_carConnected, g_battPct);
            // Heartbeat to car every 500ms
            if ((now % 500) < 20 && g_carMac[0] != 0) {
                PktHeader hb = { PKT_HEARTBEAT, RC_ID, now };
                espnow_send(g_carMac, &hb, sizeof(hb));
            }
            break;

        case RC_LOOKING:
            // Broadcast RACE_LOOKING every 500ms
            if ((now - g_lookingMs) >= LOOKING_INTERVAL_MS) {
                g_lookingMs = now;
                PktRaceLooking lk;
                lk.hdr = { PKT_RACE_LOOKING, RC_ID, now };
                memcpy(lk.rcMac,  g_ownMac, 6);
                memcpy(lk.carMac, g_carMac, 6);
                espnow_broadcast(&lk, sizeof(lk));
                g_lookingDot++;
            }
            display_looking(g_lookingDot);
            break;

        case RC_NFC_SETUP:
            display_nfc_setup(g_nfcDone, g_nfcTotal, g_isHost);
            break;

        case RC_LOBBY:
            display_lobby(g_myReady, g_oppReady, g_lobbyMode,
                          g_lobbyLaps, g_lobbyTimeSec, g_lobbyTags, g_isHost);
            break;

        case RC_RACING:
            display_racing(g_gs, now);
            break;

        case RC_FINISHED:
            // display_results already called once in dispatch
            break;

        default: break;
    }

    // ── 4. Connection LED ─────────────────────────────────────────────────────
    if (!g_carConnected) {
        // Slow blink red
        digitalWrite(PIN_LED_R, (now / 500) % 2 == 0);
        digitalWrite(PIN_LED_G, LOW);
    } else if (g_phase == RC_RACING) {
        if (g_gs.badPower != PWR_NONE) {
            // Fast blink red
            digitalWrite(PIN_LED_R, (now / 100) % 2 == 0);
            digitalWrite(PIN_LED_G, LOW);
        } else if (g_gs.flags & 0x01) { // shield
            digitalWrite(PIN_LED_R, LOW);
            digitalWrite(PIN_LED_B, (now / 200) % 2 == 0);
        } else {
            digitalWrite(PIN_LED_R, LOW);
            digitalWrite(PIN_LED_G, HIGH);
        }
    }

    vTaskDelay(1);
}

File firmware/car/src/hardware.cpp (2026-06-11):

// =============================================================================
//  hardware.cpp — Hardware driver stubs
//
//  These are skeleton implementations.
//  Fill in each function using your specific sensor libraries.
//  All pin numbers are defined in types.h.
// =============================================================================

#include "hardware.h"
#include <Arduino.h>
#include <Wire.h>
// #include <Adafruit_PN532.h>    // uncomment when wired
// #include <Adafruit_MPU6050.h>  // uncomment when wired
// #include <ESP32Servo.h>        // uncomment when wired
// #include <SD.h>                // uncomment when wired

// ---------------------------------------------------------------------------
// Motor + Servo
// ---------------------------------------------------------------------------

// static Servo g_servo;  // uncomment

void hw_motor_init() {
    pinMode(PIN_MOTOR_STBY, OUTPUT);
    pinMode(PIN_MOTOR_IN1,  OUTPUT);
    pinMode(PIN_MOTOR_IN2,  OUTPUT);
    ledcSetup(LEDC_MOTOR_CH, LEDC_MOTOR_FREQ, LEDC_RES);
    ledcAttachPin(PIN_MOTOR_PWM, LEDC_MOTOR_CH);

    // g_servo.attach(PIN_SERVO);  // uncomment
    hw_motor_enable();
    Serial.println("[HW] Motor+Servo init OK");
}

void hw_motor_set(int8_t throttle) {
    // clamp
    throttle = constrain(throttle, -100, 100);
    uint8_t pwm = (uint8_t)(abs(throttle) * 255 / 100);

    if (throttle > 0) {
        digitalWrite(PIN_MOTOR_IN1, HIGH);
        digitalWrite(PIN_MOTOR_IN2, LOW);
    } else if (throttle < 0) {
        digitalWrite(PIN_MOTOR_IN1, LOW);
        digitalWrite(PIN_MOTOR_IN2, HIGH);
    } else {
        // Brake
        digitalWrite(PIN_MOTOR_IN1, LOW);
        digitalWrite(PIN_MOTOR_IN2, LOW);
    }
    ledcWrite(LEDC_MOTOR_CH, pwm);
}

void hw_servo_set(int8_t steering) {
    // Map -100..+100 to servo angle 50..130 (centre = 90)
    int angle = 90 + (steering * 40 / 100);
    angle = constrain(angle, 50, 130);
    // g_servo.write(angle);  // uncomment
}

void hw_motor_kill()   { digitalWrite(PIN_MOTOR_STBY, LOW);  }
void hw_motor_enable() { digitalWrite(PIN_MOTOR_STBY, HIGH); }

// ---------------------------------------------------------------------------
// IR TX
// ---------------------------------------------------------------------------

void hw_ir_fire() {
    // 38kHz burst for IR_BURST_MS ms via LEDC
    ledcSetup(LEDC_IR_CH, LEDC_IR_FREQ, LEDC_RES);
    ledcAttachPin(PIN_IR_TX1, LEDC_IR_CH);
    ledcAttachPin(PIN_IR_TX2, LEDC_IR_CH);
    ledcWrite(LEDC_IR_CH, 127); // 50% duty
    delay(IR_BURST_MS);
    ledcWrite(LEDC_IR_CH, 0);
    ledcDetachPin(PIN_IR_TX1);
    ledcDetachPin(PIN_IR_TX2);
}

// ---------------------------------------------------------------------------
// IR RX (interrupt-driven)
// ---------------------------------------------------------------------------

static volatile bool s_rearHit = false;
static volatile bool s_lapTrig = false;

void IRAM_ATTR isr_rear1() { s_rearHit = true; }
void IRAM_ATTR isr_rear2() { s_rearHit = true; }
void IRAM_ATTR isr_side1() { s_lapTrig = true; }
void IRAM_ATTR isr_side2() { s_lapTrig = true; }

void hw_ir_rx_init() {
    pinMode(PIN_IR_RX_REAR1, INPUT_PULLUP);
    pinMode(PIN_IR_RX_REAR2, INPUT_PULLUP);
    pinMode(PIN_IR_RX_SIDE1, INPUT_PULLUP);
    pinMode(PIN_IR_RX_SIDE2, INPUT_PULLUP);
    attachInterrupt(digitalPinToInterrupt(PIN_IR_RX_REAR1), isr_rear1, FALLING);
    attachInterrupt(digitalPinToInterrupt(PIN_IR_RX_REAR2), isr_rear2, FALLING);
    attachInterrupt(digitalPinToInterrupt(PIN_IR_RX_SIDE1), isr_side1, FALLING);
    attachInterrupt(digitalPinToInterrupt(PIN_IR_RX_SIDE2), isr_side2, FALLING);
}

bool hw_ir_rear_hit_pending() {
    if (s_rearHit) { s_rearHit = false; return true; }
    return false;
}

bool hw_ir_lap_pending() {
    if (s_lapTrig) { s_lapTrig = false; return true; }
    return false;
}

// ---------------------------------------------------------------------------
// Accelerometer (MPU6050)
// ---------------------------------------------------------------------------

// static Adafruit_MPU6050 g_mpu;  // uncomment
static volatile bool s_accelReady = false;

void hw_accel_init() {
    Wire.begin(PIN_MPU_SDA, PIN_MPU_SCL);
    // if (!g_mpu.begin()) { Serial.println("[HW] MPU6050 not found!"); }
    // g_mpu.setAccelerometerRange(MPU6050_RANGE_8_G);
    // g_mpu.setFilterBandwidth(MPU6050_BAND_21_HZ);
    Serial.println("[HW] Accel init OK (stub)");
}

float hw_accel_read_g() {
    // sensors_event_t a, g, temp;
    // g_mpu.getEvent(&a, &g, &temp);
    // float ax = a.acceleration.x / 9.81f;
    // float ay = a.acceleration.y / 9.81f;
    // float az = a.acceleration.z / 9.81f;
    // return sqrtf(ax*ax + ay*ay + az*az) - 1.0f;
    return 0.0f; // stub
}

// ---------------------------------------------------------------------------
// NFC (PN532)
// ---------------------------------------------------------------------------

// static Adafruit_PN532 g_nfc(PIN_NFC_SDA, PIN_NFC_SCL);  // uncomment
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

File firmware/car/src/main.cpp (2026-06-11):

// =============================================================================
//  main.cpp — FPV Racer v2.0 Car Firmware
//
//  ESP32 dual-core task layout:
//
//    Core 0 (app_cpu):  setup(), loop()
//      • ESP-NOW packet dispatch
//      • Host logic / client logic (game state)
//      • NFC polling (100ms)
//      • Accelerometer processing
//      • UIState broadcast (host, 200ms)
//      • Phase state machine
//
//    Core 1 (pro_cpu):  driveTask
//      • Motor + servo (consumes DriveCmd queue, 50Hz)
//      • IR TX (on semaphore signal)
//      • IR RX polling (continuous)
//      • Lap-gate IR polling (continuous)
//
//  FreeRTOS primitives:
//    xQueueDriveCmd   — Core 0 → Core 1: (throttle, steering)
//    xSemaphoreIrFire — Core 0 → Core 1: fire IR burst
//    xQueueRxPkts     — ESP-NOW ISR → Core 0: raw incoming packets
//
// =============================================================================

#include <Arduino.h>
#include <freertos/FreeRTOS.h>
#include <freertos/task.h>
#include <freertos/queue.h>
#include <freertos/semphr.h>

#include "types.h"
#include "hardware.h"
#include "comms.h"
#include "host_logic.h"
#include "client_logic.h"

// ---------------------------------------------------------------------------
// Determine role at compile time
// ---------------------------------------------------------------------------
// CAR_ID is defined in types.h (1 or 2, set per board before flashing)
// Role assignment happens during pairing: first to receive RACE_LOOKING wins HOST
// We track runtime role in g_isHost.
static bool g_isHost = false;

// ---------------------------------------------------------------------------
// FreeRTOS handles
// ---------------------------------------------------------------------------

struct DriveCmd { int8_t throttle; int8_t steering; };

static QueueHandle_t  xQueueDriveCmd;
static SemaphoreHandle_t xSemaphoreIrFire;

// ---------------------------------------------------------------------------
// Global phase (shared, but only written from Core 0)
// ---------------------------------------------------------------------------

static volatile CarPhase g_phase       = PHASE_IDLE;
static volatile bool     g_rcConnected = false;
static uint32_t          g_lastNfcMs   = 0;
static uint32_t          g_lastStationMs = 0; // debounce station-lost detection
static uint8_t           g_ownMac[6];

// ---------------------------------------------------------------------------
// Core 1 Drive Task
//   Priority: high (configMAX_PRIORITIES - 1)
//   Stack:    4096 bytes
// ---------------------------------------------------------------------------

void driveTask(void* pvParameters) {
    hw_motor_init();
    hw_ir_rx_init();

    DriveCmd cmd = {0, 0};

    while (true) {
        // ── Apply drive command ─────────────────────────────────────────────
        if (xQueueReceive(xQueueDriveCmd, &cmd, 0) == pdTRUE) {
            // Drive modifiers are applied inside client_apply_drive()
            // (host car calls same path — it is also a driveable car)
            if (g_isHost) {
                // Host car applies modifiers locally too
                // (host PlayerState bad power is checked in client modifier logic
                //  since the host car physically executes drive the same way)
                hw_motor_set(client_throttle_modified(cmd.throttle));
                hw_servo_set(client_steering_modified(cmd.steering));
            } else {
                client_apply_drive(cmd.throttle, cmd.steering);
            }
        }

        // ── IR fire on semaphore ────────────────────────────────────────────
        if (xSemaphoreTake(xSemaphoreIrFire, 0) == pdTRUE) {
            hw_ir_fire(); // blocks for IR_BURST_MS ms — acceptable on Core 1
        }

        // ── IR rear-hit detection ───────────────────────────────────────────
        if (hw_ir_rear_hit_pending()) {
            // Signal Core 0 via a minimal queue
            // (reuse DriveCmd queue slot won't work — use a flag instead)
            // Simple atomic flag — Core 0 polls it
            extern volatile bool g_hitPending;
            g_hitPending = true;
        }

        // ── Lap gate IR detection ───────────────────────────────────────────
        if (hw_ir_lap_pending()) {
            extern volatile bool g_lapPending;
            g_lapPending = true;
        }

        vTaskDelay(pdMS_TO_TICKS(20)); // 50Hz drive loop
    }
}

// ---------------------------------------------------------------------------
// Shared flags (Core 1 sets, Core 0 clears)
// ---------------------------------------------------------------------------

volatile bool g_hitPending = false;
volatile bool g_lapPending = false;

// ---------------------------------------------------------------------------
// Pairing state machine (run inside loop() during CONNECTING phase)
// ---------------------------------------------------------------------------

static uint8_t g_oppMac[6]    = {0};
static uint8_t g_oppRcMac[6]  = {0};
static uint8_t g_ownRcMac[6]  = {0};
static bool    g_peersKnown   = false;

static void run_pairing() {
    static uint32_t lookingStart = 0;
    if (lookingStart == 0) {
        lookingStart = millis();
        comms_start_looking();
        Serial.println("[PAIR] Broadcasting RACE_LOOKING...");
    }

    // Did we receive a RACE_LOOKING from another car?
    uint8_t senderMac[6];
    if (comms_got_looking(senderMac)) {
        // First to see a peer: if we have no opponent yet, accept
        if (!g_peersKnown) {
            memcpy(g_oppMac, senderMac, 6);
            comms_stop_looking();
            comms_add_peer(PEER_OPP_CAR, g_oppMac);
            comms_send_accept(g_oppMac);

            // The car that sends ACCEPT becomes HOST
            g_isHost = true;
            Serial.println("[PAIR] Sent ACCEPT — we are HOST");
            g_peersKnown = true;
            g_phase      = PHASE_LOBBY;

            if (g_isHost) {
                host_init();
                // Move to NFC setup scan
                Serial.println("[HOST] Starting NFC tag scan...");
                host_nfc_setup_begin(10); // scan up to 10 tags
                g_phase = PHASE_NFC_SCAN;
            }
        }
    }
}

// ---------------------------------------------------------------------------
// Core 0 packet dispatcher
// Called every loop() for each packet in the ESP-NOW receive queue
// ---------------------------------------------------------------------------
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

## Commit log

2026-06-29 Update note about camera and remote assembly
2026-06-29 Update quantities for heat set inserts and screws
    [BOM.csv.csv]
